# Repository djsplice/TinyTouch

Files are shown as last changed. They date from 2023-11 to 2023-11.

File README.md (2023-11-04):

# TinyTouch Z Offset probe

## What is this thing?
It's a 'membrane potentiometer' that's typically used to register touch input, connected to an inexpensive microcontroller to more repeatably measure how far away a 3D printer nozzle is from its build surface.

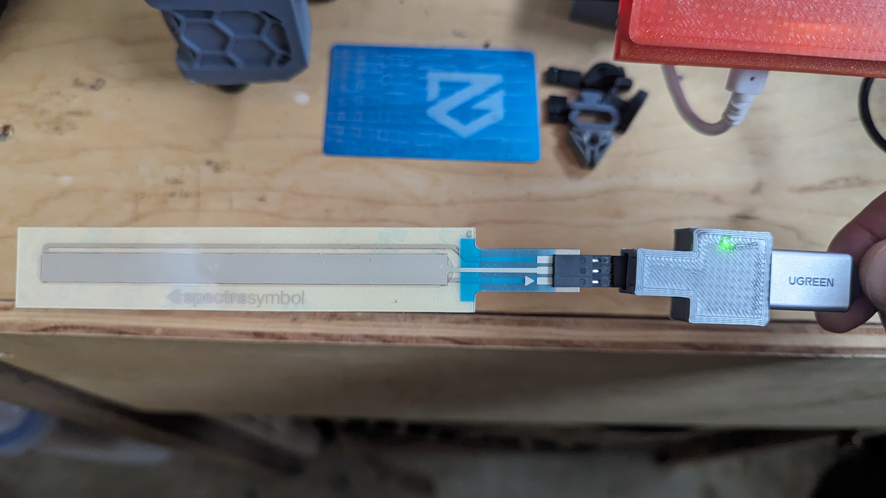
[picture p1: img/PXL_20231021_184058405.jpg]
TinyTouch


## Why this thing?
1. I wanted an easier and more repeatable way to measure my Probe Z Offset
2. I don't have enough room on my printer to use a sexbolt to enable an auto-z offset calibration 
3. I'm using a Beacon probe for a virtual z end-stop and bed mesh calibration
4. I'm using a modified EVA tool head and not very interested in moving to other solutions

## How does this thing help?
I had originally used the 'paper method' for determining Z Offset, and have struggled with it for many years... I never invested enough time to make it a repeatable process, always having to do additional steps (baby steps, many test prints, etc...) in order to get my first layer dialed in.

I recently started using an aluminum card of fixed width (a type of feeler gauge if you will) in place of a piece of paper, and it helped me improve my repeatability when measuring Z offset, however, I still needed to play around with baby stepping and test prints... Better, but not ideal. 

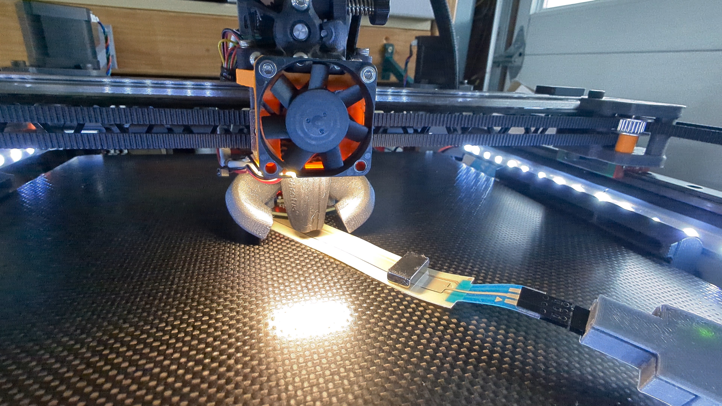
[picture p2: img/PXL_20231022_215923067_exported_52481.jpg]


## Repeatability?
I believe the variability in measurement using the paper or feeler gauge method is due to the fact that there's some subjectiveness (human feel) involved in determining just how much the nozzle is allowed to pinch the paper or feeler gauge. My guess is that this subjective measurement can introduce enough variance in measurement that it can affect first-layer consistency. 

It's amazing how much subtlety the human hand can feel!

This sensor replaces the paper or fixed-size feeler gauge when using the PROBE_CALIBRATE Klipper macro, and will consistently indicate when the nozzle is touching the bed, generally achieving a consistent z-offset measurement with a variance of +/- .01mm.

## Parts
1. [ATTiny85 Dev board](https://a.co/d/05ZdjdA)
2. [Spectra Symbol Soft Potentiometer](https://www.sparkfun.com/products/8680) (I used a 150mm, but 50mm ones work just as well) 
3. [USB extension cable](https://a.co/d/d9y83wm) for power
4. 3 Jumper wires and a 3 Pin 2.54mm pitch Dupont connector
5. A 3D printed case to hold everything together

[Spectra Symbol Soft Potentiometer Data Sheet](https://spectra-symbol-landing.s3.us-west-1.amazonaws.com/data-sheets/SoftPot-Series-Datasheet-v2019a.pdf)

## Wiring
This is a very basic circuit! We use the 5v, Ground, and P0 pins from the ATTiny85 dev board and connect them to a 3 pin JST connector (male in this instance).

From left to right the pin outs go 5v - Sensor Pin (P0) - Ground - corresponding with the Softpot pins.

* I ended up cutting about 3cm of jumper wire, and crimping the JST connectors before soldering.
* Once soldered, I fed the pins through the hole where the plastic JST conector will go, inserting the wires into the JST housing in the correct order (5v - Sensor Pin - Ground)
* This should provide enough length to insert the JST housing over the pins and into the 3D printed case

## Programming
I've included the code and the VSCode / platform.io scaffolding used to help me program the ATTiny85 Dev Board. I'm pretty new to using VSCode and Platform.io to program microcontrollers, so I don't have any useful advice to share outside of this:
- I needed to set the following value in the `platformio.ini` to successfully upload code to the ATTiny85 dev board 
   -  `upload_protocol = micronucleus` 

## Printing the Case
* I modified an ATTiny85 case originally found here: https://www.printables.com/model/52250-case-for-digispark-attiny85
* You will find the top/bottom parts of the cases in the stl folder

## Usage
I've tested this with a Beacon probe, though I assume it will also work with other probes, but configuration fields will vary.

### Configure Klipper
In the `[beacon]` section of your `printer.cfg` add the following line:

    `cal_nozzle_z: 0.48`

This value is the thickness in mm of your soft potentiometer... It probably doesn't hurt to measure your specific potentiometer as it may have a slightly different value.

### `PROBE_CALIBRATE`
1. Make sure  your nozzle is clean and free of filament. If you've got any dried on filament stuck to your nozzle, you won't get an accurate measurement!
1. If your nozzle is squeaky clean - Run the `PROBE_CALIBRATE` klipper macro.
1. Slowly lower the nozzle until it just touches the soft potentiometer and the red LED on the ATTiny85 lights up.
    - Jamming the nozzle into the potentiometer could cause permanent damage by crushing the thin film actuator, go slow, and ideally in small increments!
1. Back off the nozzle in .01mm increments until the red LED turns off
1. Lower the nozzle again by .01mm until the red LED lights up - this should help you obtain a repeatable offset measurement of about .01mm
1. Accept the offset value, save config and restart the firmware

Enjoy your perfect first layer! 

## Photos
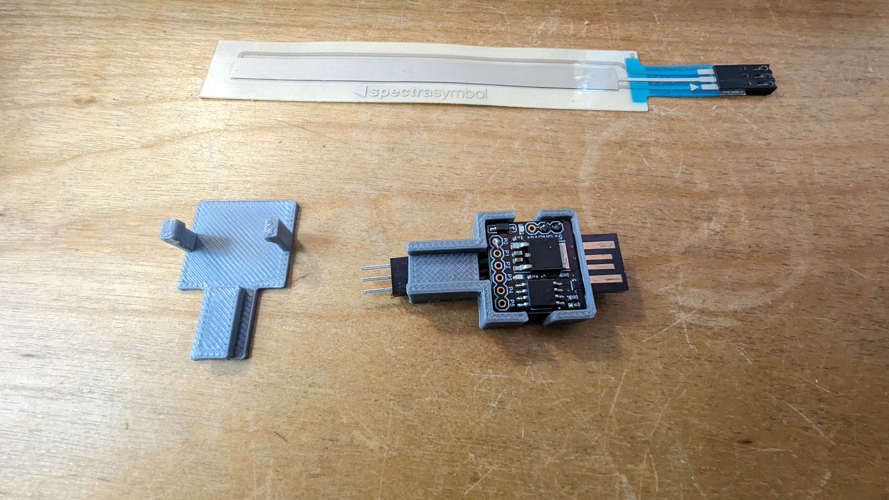
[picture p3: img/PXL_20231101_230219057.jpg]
Assembled

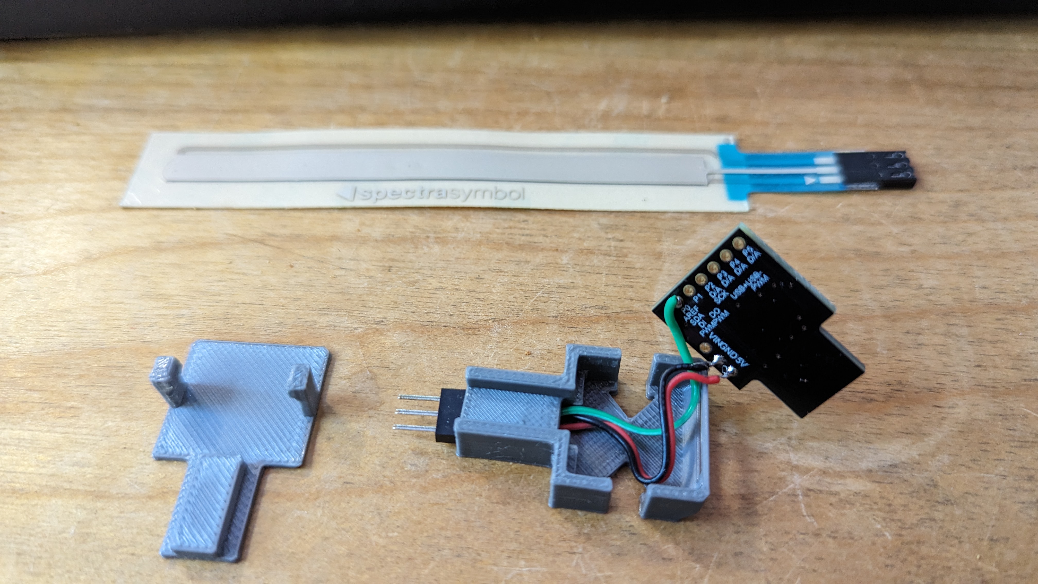
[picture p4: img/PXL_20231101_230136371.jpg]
Back Side


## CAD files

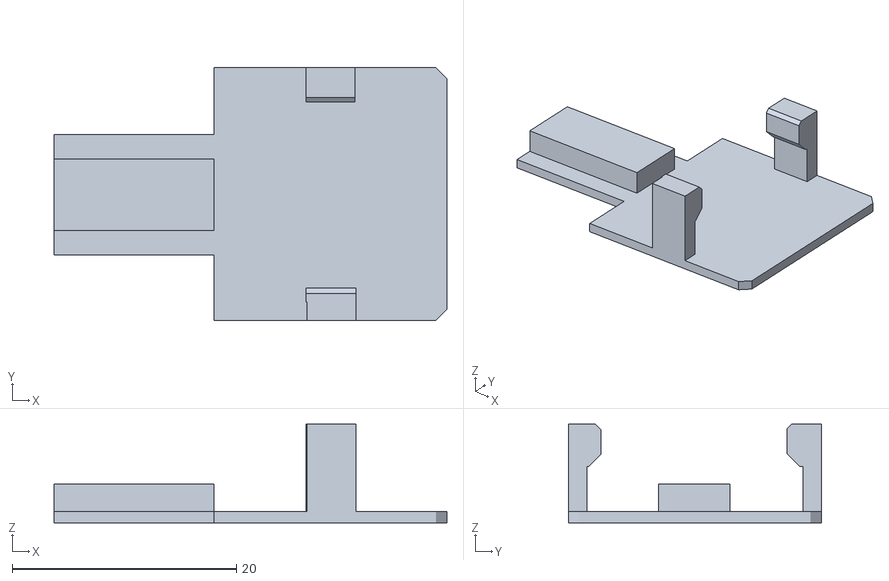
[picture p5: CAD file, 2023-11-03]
stl/case-top.stl
35.1 x 22.6 x 8.80

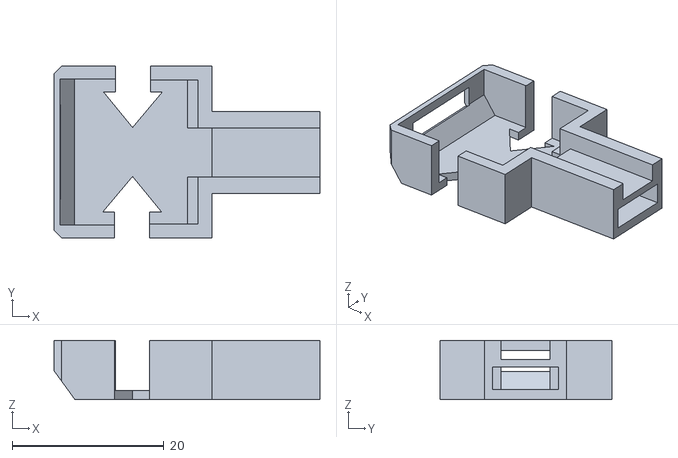
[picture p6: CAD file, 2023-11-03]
stl/case-bottom.stl
35.1 x 22.6 x 7.80

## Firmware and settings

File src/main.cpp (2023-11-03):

#include <Arduino.h>
#define sensePin 0
#define internalLED 1
int digitalPinVal = 1;

void setup() {
  pinMode(internalLED, OUTPUT); //set PB1 (PWM1) as output INTERNAL RED LED 
  pinMode(sensePin, INPUT_PULLUP);
}

void loop() {
  // Read the digital IO pin - state LOW (Touched) HIGH (Open)
  // Soft potentiometer will reduce current to zero if touched at the end away from the wires
  // Normal state is high (Open, no touch), input pin is pulled high

  digitalPinVal = digitalRead(sensePin);
  if (digitalPinVal < 1){
    // Touch detected - Turn on the RED LED
    analogWrite(internalLED, 255);
    // Wait for a quarter second
    delay(250);
  }else{
    // No Touch detected - Turn the RED LED OFF
    analogWrite(internalLED, 0);
  }
}
